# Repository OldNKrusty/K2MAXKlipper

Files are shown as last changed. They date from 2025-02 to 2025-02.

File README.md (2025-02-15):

# K2MAXKlipper

Klipper installation on Anycubic Kobra 2 MAX with minimal cost or modification

A simple, easy and cost effective solution to install full mainline Klipper on your Anycubic Kobra 2 MAX.  
This will keep as many original parts as possible by replacing only the mainboard with a genuine Anycubic mainboard from a Kobra 2 coupled with minor physical modifications to the case and 3 connectors.

This is a great project for a weekend when you can focus and will not need your printer.  
Everything CAN be done in one day but it is best not to rush.  
Take your time and be VERY clear with what you are doing. Read the instructions below multiple times to be sure you are familiar, and comfortable, with all steps before you begin to do ANYTHING.  
If you have modified 3D printers previously this should be a very simple mod for you.  
If you have not modified a 3D printer before, but you enjoy using simple hand tools, you should have no trouble.  
Just go slow, read the instructions, and pay very close attention to what you are doing.  Take pictures along the way to help you keep track of the way things are BEFORE you disconnect anything in case you wish to reverse any of the mods.  
But most of all HAVE FUN!!!!!!

Please pay special attention to the section on the accelerometers.  
This is an OPTIONAL modification.  
You do NOT have to remove the bed accelerometer if you do not want to but at this stage BOTH the bed and printhead accelerometers will be disabled by this modification.  
This project is not fully completed and the intention is to get the stock accelerometers to work with the replacement mainboard.  
Until then a USB-C accelerometer (I use a BTT S2DW) is a simple solution to be able to set your input shaping calibrations.

---

## Modification instructions  

Please pay special attention to the secton on the accelerometers.  This is an OPTIONAL modification.  You do NOT have to remove the bed accel

Parts required:
- [Trigorilla_PRO_B_V1.0.2](https://1coderookie.github.io/Kobra2Insights/hardware/mainboard/#trigorilla-pro-b-v_102-stock) mainboard
- Raspberry Pi or Pi alternative to run Klipper(I use a BTT Pi adapter with CB1 board but an older laptop running Linux will work perfectly fine as well)
- Hole cutout template and cover plate (3D print them from included STLs)

Tools Required:

- 2.5mm Allen/hex wrenches
- Digital multimeter with continuity mode
- Dremel tool with fiberglass cutoff wheels
- Small fine file
- Super glue
- A working 3D printer to print off required parts (you can print them on your MAX before you do the mod)
- xacto knife to trim connectors (I prefer #11 blade)
- zip ties for cable management
- double sided tape

These instructions are intended to help make it simple and very inexpensive to convert your Kobra 2 MAX to run full mainline Klipper.  
The ONLY part that will need to be purchased (assuming you already have a Pi or equivalent) is the mainboard.  
I specifically did this project in this way so I could use my spare Trigorilla_PRO_B_V1.0.2 from my Kobra 2 (Marlin version) which has also been upgraded to Klipper because when it comes down to it I am very cheap and hate buying things I don't need to.  lol  

Using this board will also require the minimal amount of physical modification to the printer case and connectors AND it means that ONLY Anycubic parts and electronics will be used...so technically this is still an Anycubic printer, just how it SHOULD have been done by Anycubic in the first place.  
It also has the exact same hole pattern/spacing as the stock mainboard which makes installation very simple with NO additional hardware required.  
Please also note that this project is not 100% completed yet and as changes are made or new information comes to light these notes and instructions will be updated accordingly.

PLEASE BE AWARE:  This modification as it currently stands will also remove the functionality of the built in accelerometers in both the printhead and bed.  
This is NOT a permanent change however and plans are in place to figure out how to incorporate the stock accelerometers into this modification.  
The one in the bed CAN be removed and repurposed for input shaping but I chose to use the BTT 2SWD USB-C accelerometer I already had on hand (USB-C is SO much easier to connect).  
I will leave up to you to decide what you find to be best for YOUR application.  
Just be warned before you go ahead with this mod if this is going to be an issue for you.  
This modification will also disable the LCD functionality but you can either add your preferred screen to your Pi or use the mainsail web interface (my preferred choice), or fluid, if you prefer.

To begin you will need to print off the hole cutout template to locate the hole you will need to cut in the front of the case to allow for the SD card slot and USB-C port.  
You will also need to print off the cover plate to fill the hole and provide a cleaner look.  
Both STLs have been included.  
To properly locate the template simply place a small piece of double sided tape on the side facing AWAY from the board, slide it over the USB-C port and SD card slot and then place the new board onto the existing mounting holes (image 1).  

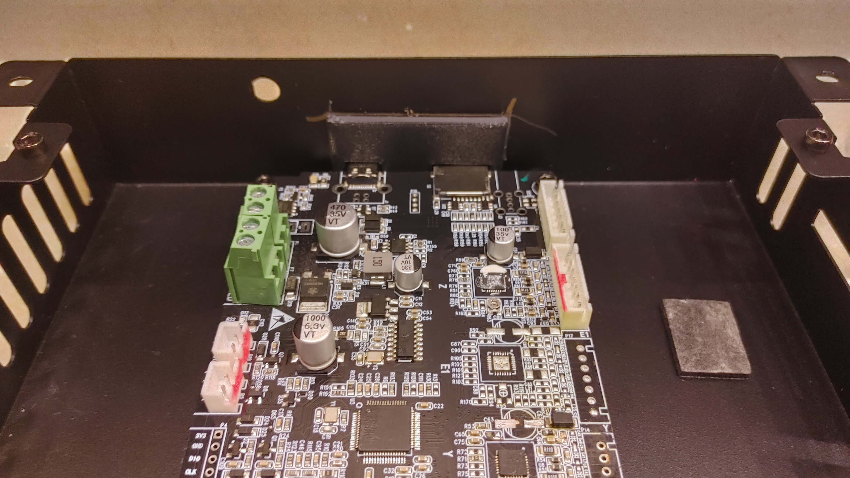
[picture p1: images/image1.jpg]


Be sure to line up the mounting holes as best as possible.  
When the board is properly located and mounted press the template against the inside of the case to allow the double sided tape to hold it in place (image 2).  

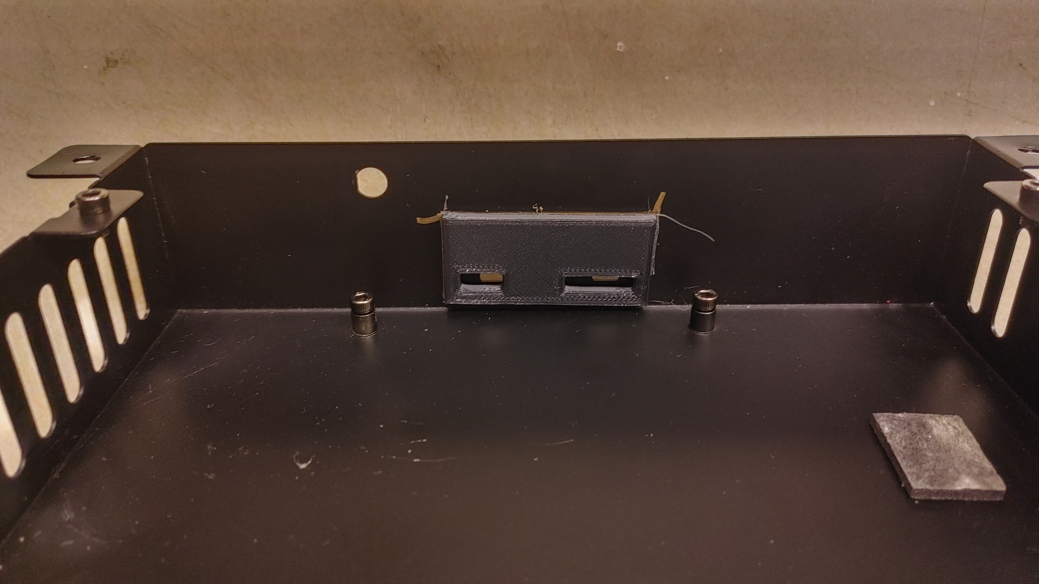
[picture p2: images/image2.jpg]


Remove the board and trace/scribe around the perimeter of the template to mark your cut lines.  
I found it easiest to cut with a Dremel tool and fiberglass cutoff wheel directly on the scribed lines to allow for a little bit of "wiggle room" when installing the cover plate.  
Once the hole is cut be sure to file the rough edges to remove any burrs or jagged edges and then fully clean the case, inside and out, to remove ALL traces of metal shavings.  
This is critical to prevent any short circuits on the board.

Now mount the new board on the existing stand-offs and use the original screws to secure it.  
Do not tighten the screws completely as you may need to adjust position slightly.  
Place the cover plate you printed into the hole you just cut, lining up the SD card slot and USB-C port. Position the cover plate so that the bottom edge is flush with the edge of the case (image 3).  

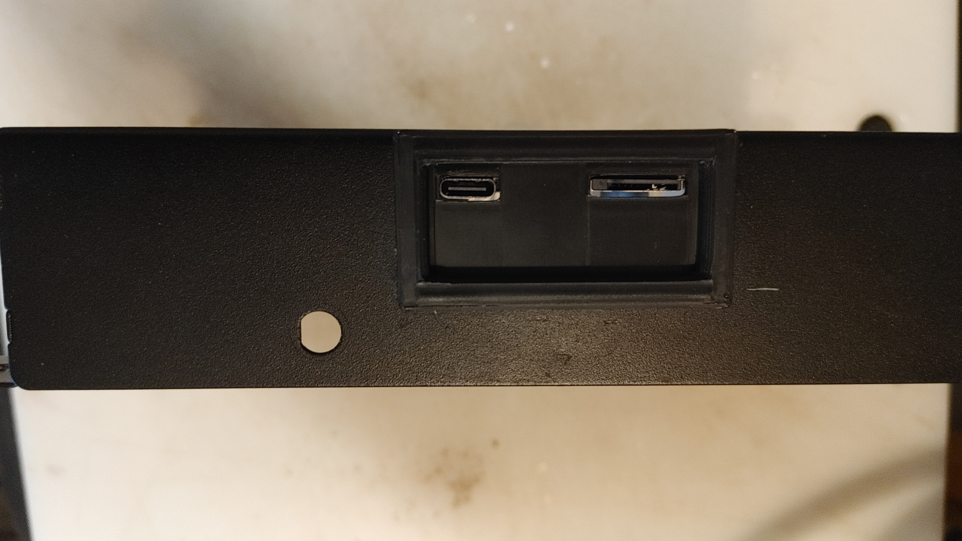
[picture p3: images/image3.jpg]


Use your favourite glue to permanently attach the cover plate to the face of the case.  
I used cheap dollar store super glue but 5 minute epoxy would be a great choice as well.  
I would advise inserting a USB-C cable into the USB-C port first to make sure it is properly aligned to make future insertion easy.  
Once you have applied the glue use small clamps or painters tape to hold it in place so you can remove the screws holding the board in the case, and then CAREFULLY remove the board to prevent ANY glue or residue from contacting the board.  
Leave it to fully dry/cure (I left it overnight) and then remove the clamps to see the finished result (image 4).  

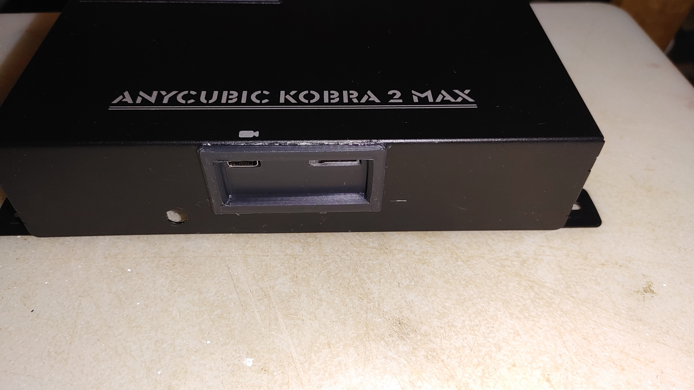
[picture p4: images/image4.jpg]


That is all for the board replacement and case modifications.

new board installed

Now you need to modify the wire harness to the printhead. The mainboard end connector of the wire harness will need to be modified but the printhead connector will be left as-is and this will allow you to use the stock red ducted printhead.  
As the replacement mainboard has a 22 pin connector and the original mainboard (which has now been removed) uses a 24 pin connector you will have to trim one pair of pins off of the edge of the connector.  
It is best to remove ALL pins from the connector first as you will need to do this anyway to match the pinout of the new board.  
To remove the pins from the connector you will need to press down gently on the small tab that locks the pin in place while GENTLY pulling on the wire connected to THAT specific pin.  
Be VERY careful and only use just enough pressure to get the job done.  
You do NOT want to damage any of the pins.  
Go slow and once the pin starts moving pull it out of the connector and stop putting pressure on it.  
Start at one end of the connector and just go pin by pin until all are removed.  
You do not need to worry which pin is which at this point.  
Just get them all removed without damaging any.  
If you need to use ANY force STOP!!!!  
Once the tab is pressed down enough the pin will slide out easily.

Trim off the edge of the connector that faces the outer edge of the board and use the xacto knife to take off small slices at a time until you can fit the connector back into the connector on the board.  
I went a LITTLE too far and cut into the pin slot but this didn't cause any issues.  
Don't do what I did and try to take too much off at a time (image 5).  

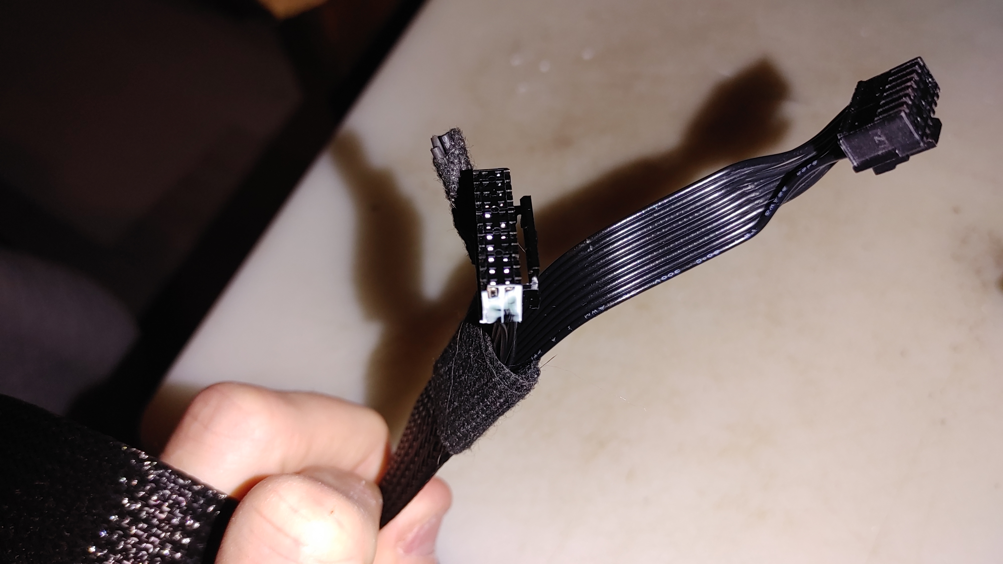
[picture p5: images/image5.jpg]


Again, go slow and be careful not to cut yourself. Ask me how I know.

With the pins all removed and the connector trimmed you will now need to match the pinout from the printhead side connector to the pinout of the new mainboard.  
Due to the differences in the printhead boards from the old and new printheads (ie older style black duct using the V0.1.5 board and new red ducted style using the V1.0.1 board) we MUST change the pin placement in the mainboard end connector of the wire harness. 

**WARNING:**    
Failure to match the pins correctly WILL result in printhead board and/or mainboard damage so take your time, follow the colour coding and test with a multimeter in continuity mode MULTIPLE times.  
This part MUST be done correctly and WILL be the single most critical part of this printer modification!!!!!!!!  
Please pay VERY close attention to the orientation of the connectors as shown in image 6.  

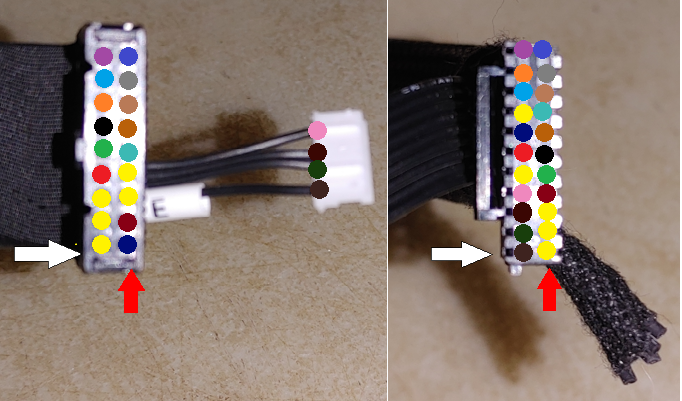
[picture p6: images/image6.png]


The images are of the connectors face on with the key/locking tab facing the left side.  
Be sure to match this orientation when looking at your connectors.  
I cannot stress this enough!!!! 

The printhead board uses an 18 pin connector whereas the new mainboard uses a 22 pin connector.  
The old mainboard you removed uses a 24 pin connector and we have to get them all to play nicely with each other.

With the pins fully removed from the mainboard connector do a simple continuity check on both ends one pin at a time.  
Follow the colour code in image 6 one pin at a time beginning with pin 1 on the printhead connector (left side of image 6) and move upwards, over to the right side and then downwards until all pins have been moved.  
Pin 1 on both connectors is marked with the white arrow.  
Pin 18 on the printhead connector and pin 22 on the board connector are marked with the red arrow.  
Start at pin 1, find the corresponding free pin on the other end and insert that pin into the appropriate hole on the mainboard side connector (the one you removed the pins from) that is marked with the same colour dot.  
For example pin 6 on the printhead connector is marked with a black dot and its corresponding hole on the mainboard connector is pin 17.  

*Please note:*  
The pins marked with yellow dots (5 in total) are NOT CONNECTED/UNUSED.  
You should NOT add any pins to these locations.  
As well, due to the differences in the printhead board versions, the old style has the extruder motor pins included (right side of image 6) in the printhead connector whereas the newer style has a separate stepper motor connector (left side of image 6).  
There WILL be 5 pins that will NOT be used (shown wrapped in tape on the right side of image 6) and these are for the accelerometer built into the V1.0.1 printhead board. This accelerometer WILL BE DISABLED because of this modification!!!  
Be sure to wrap each pin individually with electrical tape or use heat shrink tubing to make certain they do NOT touch.  
Do NOT cut these pins off!!!

Once you have placed the appropriate pins into the appropriate spots in the board connector I STRONGLY advise you to do a continuity test on each pin, going over the entire connector, 2 to 3 times (at a minimum) to be 100% certain that you have properly matched the pinout colour coding shown in image 6.  
DO NOT SPEED THROUGH THIS STEP!!!!! I CANNOT stress this enough!!!

The only other modifications REQUIRED are to the Z motor connectors.  
The new board uses a 7 pin connector but the cables have a 4 pin connector with 2 alignment tabs.  
You will need to trim off the one tab where the red arrows in image 7 are pointing.   

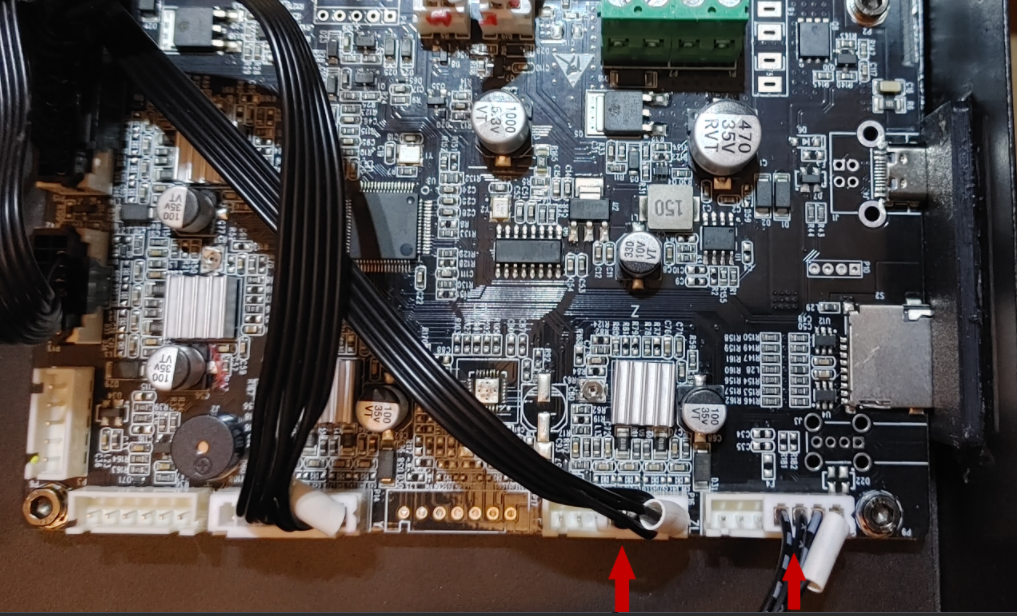
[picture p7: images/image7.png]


Be sure to insert the connectors as shown in image 7.  
The 3 unconnected pins are not used. Do not simply try to force the connector in unmodified as you stand a VERY good chance of damaging the board connector or the board itself.

An OPTIONAL, but not required, modification (I chose to do this) is to remove the accelerometer and calibration button from the bed as they will not be used with Klipper at this stage in this project.  
You can leave these in place if you wish but you will get a cleaner look by removing them.  
You will need to slip all of the cables out of the mesh sheath of the bed cable harness and separate the power wires and thermistor wires from the others.  Slide the bed power cables and thermistor wires back through the mesh sheath and properly secure to the strain relief connector on the bed using a zip tie.  Put the other cables aside as you will not need them.  
Be VERY careful not to damage the solder joints here or else you will need to repair them by resoldering.  
Due to the large mass of the bed you WILL need a powerful soldering iron (at least 60W) to effectively melt the solder.  
It's best to just avoid having to do this.  
There is a 2 pin connector soldered to the bed that connects the calibration button.  
This can be simply clipped off at the solder joints or you can choose to desolder if you wish.

Now...all you have to do is put the cabling back to where it goes on the board.  
The connectors inside the case are all labeled and go into the appropriately labeled mainboard connector (ie TO wire into TO port on the board) until they are all done.  
You can remove the LCD ribbon cable and LCD screen as these will not be compatible with Klipper and therefore not used.  
Please pay special attention to the connectors for the TO and case fan as they are directly beside each other and are exactly the same.  
Again...pay close attention to the labels on the mainboard.

Once you are done you should have the following parts removed from the printer: LCD ribbon cable, LCD screen, mainboard, and optionally: bed calibration button with built in accelerometer, calibration button cable (2 pin) and accelerometer cable (6 pin).  
You can save them all in a safe place in case you wish to return this printer back to stock (except for the hole you cut in the case and the trimmed connector of course) or you can choose to resell and recoup some of the costs (ie new mainboard and Pi alternative).

All images, STLs, printer.cfg and additional notes have been included in the zip file.  
Please feel free to modify the STLs to suit your liking.  
If you have any questions regarding this project please feel free contact me on Reddit (OldNKrusty) or by email at atomicmoped@hotmail.com

If you didn't come across it yet, visit [Kobra2Max Insights](https://1coderookie.github.io/Kobra2MaxInsights/) - it's a comprehensive infosite specifically about the Kobra 2 Max.  

Enjoy your new Klipperized Kobra 2 MAX.  

---

## Additional notes  

- As well it appears that the original Trigorilla_SPE_A_V1.0.0 mainboard (to be referred to as SPE going forward) uses genuine TMC2209 stepper driver ICs whereas the replacement Trigorilla_PRO_B_V1.0.2 board (to be referred to as PRO_B) uses GC6609 stepper driver ICs and the two are not 100% setting compatible/interchangeable but they are pin compatible.  
If a driver IC fails they SHOULD be able to be directly replaced with genuine TMC2209 ICs.

- The default acceleration value of 10000 with the SPE is FAR too high and will cause issues, specifically on the Y axis.  
The PRO_B max acceleration should be capped at 3000 in the printer.cfg file.  
I personally chose to cap my max acceleration at 2500.  
Due to the large mass of the bed I have no expectations of printing at breakneck speeds.  
I would prefer my prints to succeed slowly than fail quickly.

- You WILL also need to manually set the VRef for each stepper driver to ensure the correct current for each axis.  
Please start with the below START values and adjust as you see fit without exceeding the MAX values.  
If you find the motors begin running hot and start skipping steps you will need to lower the VRef in 0.02V increments.  
Lowering by more than 0.25V is not advised as this will lower the current too much.  

  | START Vref | MAX Vref |
  |:----------:|:--------:|
  | E: 0.60V = 0.75A | E: 0.64V = 0.8A |
  | X: 0.96V = 1.2A | X: 1.12V = 1.4A |
  | Y: 1.28V = 1.6A | Y: 1.52V = 1.9A |
  | Z: 1.12V = 1.4A | Z: 1.44V = 1.8A |  

  (Note: Z dual steppers running in parallel = 0.9A for each stepper)

- You WILL need to ensure adequate case cooling so please be certain to leave enough room for the case fan to ventilate the case.  It is also not a bad idea to replace the stepper driver heatsinks with larger 10*10*10mm heatsinks to increase the mass and surface area for better IC cooling ESPECIALLY if you are running higher currents.  
Setting motor current too high can significantly increase the temperature and dramatically shorten the life of the stepper driver ICs. Use or larger, higher mass heatsinks can HELP mitigate this but not eliminate it. I would advise using Vref as close to the START settings noted and printing slower to maximize stepper driver life.

- Even though the heated bed does come with a minimal amount of insulation I HIGHLY advise adding an aluminized foam insulation to help retain heat and reflect it back into the bed.  
This will help the bed heat faster and remain at a stable temperature.  
It will also help prevent the heat from being radiated to the top of the case and this in turn will keep the case internals cooler.  
I use a 1/4" thick self-adhesive aluminium backed foam designed for sound deadening and thermal insulation in automobiles. Similar to this: https://www.amazon.com/Car-Heat-Sound-Deadening-Insulation/dp/B0BNPZZ71X/ref=sr_1_4?sr=8-4

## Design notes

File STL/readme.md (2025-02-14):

Here you find the STL files for printing the parts mentioned in the description.

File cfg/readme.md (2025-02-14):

Here you find the `printer.cfg` file, which contains the configuration settings, pin assignments and so on.

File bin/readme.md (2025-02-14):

Here you find the `klipper.bin` file (already being renamed to `firmware.bin`) to flash Klipper the TriGorilla PRO B_v1.0.2.  

Copy the file onto your printer's mSD card and reboot the printer to initiate the flashing process.

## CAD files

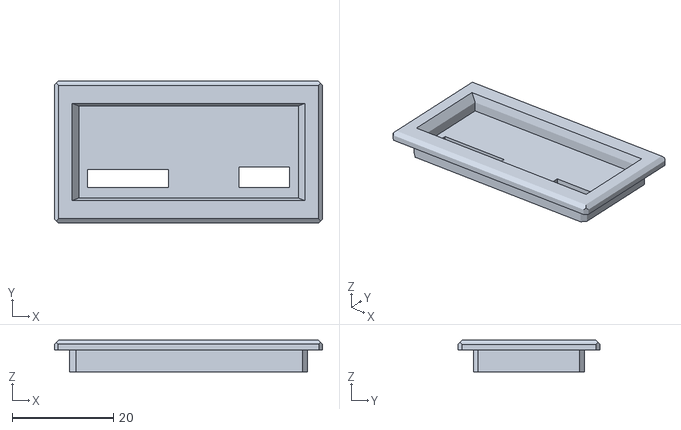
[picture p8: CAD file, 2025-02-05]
STL/Kobra 2 Max USB Cover Plate.stl
53.0 x 28.0 x 6.30

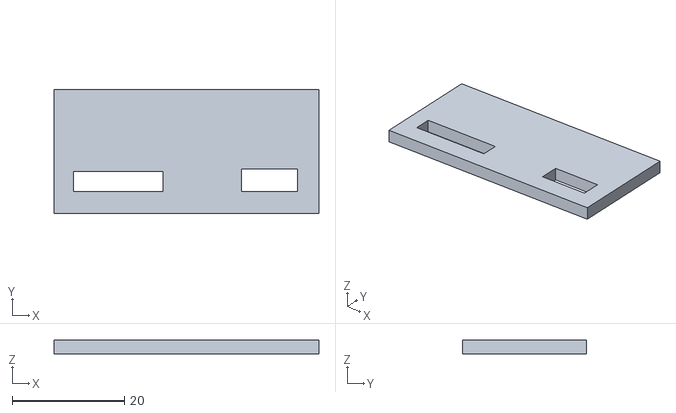
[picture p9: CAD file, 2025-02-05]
STL/Kobra 2 Max Cutout Template.stl
47.3 x 22.2 x 2.50

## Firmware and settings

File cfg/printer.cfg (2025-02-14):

# This file contains a configuration for the Anycubic Kobra2 MAX printer with a TriGorilla PRO B_v1.0.2 mainboard.
#
# See docs/Config_Reference.md for a description of parameters.
#
# To build the firmware, use the following configuration:
#   - Micro-controller: Huada Semiconductor HC32F460
#   - Communication interface: Serial (PA3 & PA2)
#   - Application address should be 0x008000.  If this does not work for you try 0x100000
#   - Baud rate for serial port 115200
#
# Installation:
#  1. Rename the klipper bin to `firmware.bin` and copy it to an SD Card.
#  2. Power off the Printer, insert the SD Card and power it on.
#  3. The printer should beep around 6 times.  Wait at least 1 minute before powering off the board and then remove the SD card.
#
# Do not set max_accel above 3000 as this will cause motor stuttering.  2000-2500 would be the maximum I would advise.


# [include macros.cfg]
# [include slot.cfg]
# [include common.cfg]


[mcu]
serial: /dev/serial/by-id/usb-1a86_USB_Serial-if00-port0
restart_method: command



[printer]
kinematics: cartesian
max_velocity: 500
max_accel: 2500
max_z_velocity: 80
max_z_accel: 2500
square_corner_velocity : 8

[output_pin power_ctrl]
pin: PB4
value: 1


[stepper_x]
step_pin: PA5
dir_pin: PA4
enable_pin: !PC3
microsteps: 16
rotation_distance: 40
endstop_pin: !PA6
position_min: -5
position_endstop: -5
position_max: 430
homing_speed: 70
homing_retract_dist : 15


[stepper_y]
step_pin: PC4
dir_pin: !PA7
enable_pin: !PC3
microsteps: 16
rotation_distance: 40
endstop_pin: !PC5
position_min: -5
position_endstop: -5
position_max: 430
homing_speed: 70
homing_retract_dist : 20


[stepper_z]
step_pin: PC7
dir_pin: !PC6
enable_pin: !PC3
microsteps: 16
rotation_distance: 8
#endstop_pin: PB8
endstop_pin: probe: z_virtual_endstop
#position_endstop: 0
position_min: -5
position_max: 501
homing_speed: 10


[extruder]
max_extrude_only_distance: 200
max_extrude_only_velocity: 60
max_extrude_only_accel: 3000
max_extrude_cross_section: 5
step_pin: PC14
dir_pin: PC15
enable_pin: !PC3
microsteps: 16
gear_ratio: 10:40
rotation_distance: 1.65914
nozzle_diameter: 0.40
filament_diameter: 1.750
heater_pin: PA1
sensor_type: EPCOS 100K B57560G104F
sensor_pin: PC1
min_extrude_temp: 0
#control: pid
#pid_kp: 22.20
#pid_ki: 1.08
#pid_kd: 119.0
min_temp: 0
max_temp: 275
pressure_advance = 0.0

[firmware_retraction]
retract_length: 1
retract_speed: 40
unretract_extra_length: 0.00
unretract_speed: 40

[heater_bed]
heater_pin: PA0
sensor_type: ATC Semitec 104GT-2
sensor_pin: PC0
#control: pid
#pid_kp: 97.1
#pid_ki: 1.41
#pid_kd: 1675.16
min_temp: 0
max_temp: 110

[filament_switch_sensor runout]
pause_on_runout: True
switch_pin: !PC13

[heater_fan controller_fan]
pin: PA14

[heater_fan hotend_fan]
pin: PA13

[fan]
pin: PB9

[probe]
pin: PB8
x_offset: 23
y_offset: -12
z_offset: 0.00


[safe_z_home]
#home_xy_position: -4, -6
home_xy_position: 0, 0
speed: 70
z_hop: 10
z_hop_speed: 10
move_to_previous: False

[bed_mesh]
speed: 60
horizontal_move_z: 5
mesh_min: 20, 0
mesh_max: 405, 405
algorithm: bicubic
bicubic_tension: 0.5
probe_count: 11, 11
fade_start: 1
fade_end: 10
fade_target: 0


[output_pin beeper]
pin: PB5
pwm: True
value: 0
shutdown_value: 0
cycle_time: 0.001


[input_shaper]
#shaper_type_x = mzv
#shaper_freq_x = 0
#shaper_type_y = mzv
#shaper_freq_y = 0

#*# <---------------------- SAVE_CONFIG ---------------------->
#*# DO NOT EDIT THIS BLOCK OR BELOW. The contents are auto-generated.
#*#
#*# [extruder]
#*# control = pid
#*# pid_kp = 17.941
#*# pid_ki = 0.647
#*# pid_kd = 124.464
#*#
#*# [heater_bed]
#*# control = pid
#*# pid_kp = 72.782
#*# pid_ki = 0.827
#*# pid_kd = 1602.103
#*#
#*# [stepper_z]
#*# position_endstop = 3.550
#*#
#*# [probe]
#*# z_offset = -1.150
#*#
#*# [input_shaper]
#*# shaper_type_x = mzv
#*# shaper_freq_x = 54.6
#*# shaper_type_y = ei
#*# shaper_freq_y = 49.4
#*#
#*# [bed_mesh default]
#*# version = 1
#*# points =
#*# 	-2.245000, -2.240000, -2.200000, -2.117500, -2.060000, -2.057500, -1.990000, -1.917500, -1.932500, -1.922500, -1.895000
#*# 	-2.057500, -2.005000, -1.992500, -1.880000, -1.832500, -1.855000, -1.742500, -1.685000, -1.692500, -1.662500, -1.722500
#*# 	-1.857500, -1.887500, -1.870000, -1.792500, -1.745000, -1.742500, -1.680000, -1.602500, -1.610000, -1.595000, -1.557500
#*# 	-1.727500, -1.702500, -1.697500, -1.595000, -1.555000, -1.527500, -1.485000, -1.447500, -1.455000, -1.420000, -1.450000
#*# 	-1.605000, -1.652500, -1.640000, -1.575000, -1.540000, -1.562500, -1.590000, -1.492500, -1.467500, -1.427500, -1.367500
#*# 	-1.497500, -1.495000, -1.515000, -1.437500, -1.440000, -1.530000, -1.502500, -1.397500, -1.367500, -1.300000, -1.300000
#*# 	-1.410000, -1.495000, -1.517500, -1.480000, -1.480000, -1.525000, -1.505000, -1.422500, -1.400000, -1.352500, -1.275000
#*# 	-1.405000, -1.425000, -1.460000, -1.405000, -1.415000, -1.472500, -1.395000, -1.327500, -1.302500, -1.235000, -1.225000
#*# 	-1.472500, -1.560000, -1.577500, -1.535000, -1.522500, -1.550000, -1.502500, -1.420000, -1.405000, -1.357500, -1.235000
#*# 	-1.565000, -1.575000, -1.602500, -1.530000, -1.515000, -1.555000, -1.450000, -1.375000, -1.347500, -1.257500, -1.225000
#*# 	-2.135000, -2.177500, -2.162500, -2.112500, -2.072500, -2.042500, -1.955000, -1.862500, -1.800000, -1.682500, -1.562500
#*# x_count = 11
#*# y_count = 11
#*# mesh_x_pps = 2
#*# mesh_y_pps = 2
#*# algo = bicubic
#*# tension = 0.5
#*# min_x = 20.0
#*# max_x = 405.0
#*# min_y = 0.0
#*# max_y = 405.0
